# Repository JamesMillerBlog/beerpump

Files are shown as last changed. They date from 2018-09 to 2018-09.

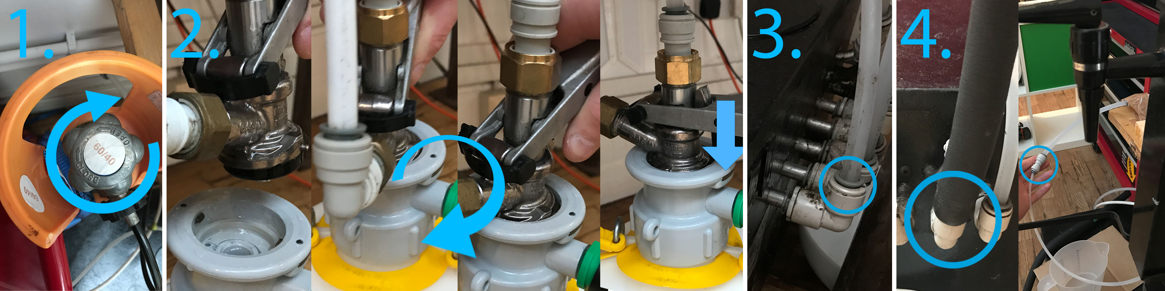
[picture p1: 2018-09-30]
Arduino-code/beerSetup.jpg

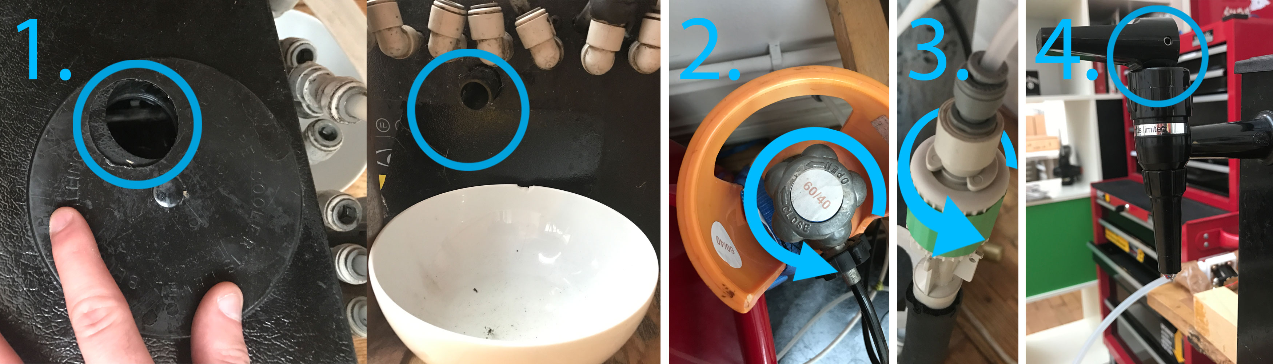
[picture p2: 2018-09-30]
Arduino-code/beerPour.jpg

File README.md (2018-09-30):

# BEER PUMP SET UP INSTRUCTIONS #

This is a tutorial on how to set up the beer pump hardware and software.

## Index ##
1. Code set up
2. Hardware set up
3. Beer equipment set up
4. How to operate
5. How to integrate software into the front end and hardware into the beer font
6. Troubleshooting

## 1. Code set up ##

### Code logic ###

This program is run on a node express server, which serves a web page that users interact with (on the touch screen), an admin web page (which allows the use of a manual override to all functions) and the control of the electronics that regulates the valve, monitors the volume of liquid passing through the beer font and switches the LEDs on/off.

The whole application is wrapped up inside of a gulp task management system, which creates a link that users can use to access the local host through a local network (I will go into more detail about this on the 'How to Operate' section). The flow of the application is as follows:

1. The express server is launched, the locally hosted accessible links are generated and the application begins constantly checking for the state of the liquid flow sensor pin.
2. When a user clicks on the "Pour Pint" button, this fires two web sockets, one that tells the application to open the valve and another that tells the application that it is pouring a pint. Upon receiving these sockets, the server sends a web socket back to the front end saying that the pint is being poured, then the front end responds by changing the interface.
3. As the beer is flowing, a sensor in the flow meter spins around on a 'windmill like' mechanism. As this mechanism spins around, the state of pin 2 of the Arduino goes from 1 - 0, the flow rate of the beer is calculated from the number of times the state of pin 2 **falls from 1 - 0** every 10th of a second. The ammount of beer in ml is then calculated based off of the flow rate.
4. When the "Stop Pint" button is pressed, it knows that a pint was pouring from the previous web socket message, so it sends a socket message to shut the beer valve + a socket message to state the pint has been paused and changes the interface to display "Resume Pint" + "Cancel Pint".
5. If the user presses "Resume Pint" the front end sends two socket messages to open the valve and tells the back end that the pint pouring has been resumed - the flow sensor will pick back up from where it left off.
6. If the user presses "Cancel Pint" this keeps the valve closed and all variables + functions in the backend are then reset, ready to pour a new pint.

### Downloading the code ###

Download this repository to a folder on your computer.

### Setup dependencies ###

* Install the latest version of Node onto your computer, older versions may not be able to run the dependencies needed to make the application work.

* Open Terminal from the applications folder

```
sudo npm install gulp -g
```

* Install Gulp globally

```
cd {YOUR/PATH/}
```

* Type cd into the terminal window, drag the folder that you've just downloaded into the window and press enter on your keyboard.

```
sudo npm install
```
* Type "sudo npm install" and press enter, this will install all necessary dependencies to run the application.

### Run the software ###

* Plug in the Arduino via the USB port (see below on how to set up the arduino's hardware)

```
gulp
```

* Type "gulp" into the terminal window, after a few seconds it will launch the application and open a web page. The opened web page is the touch screen interface which will need integrating with the front end, to access the admin page add the string "/admin" at the end of the url.

## 2. Hardware set up ##

### The Arduino code ###
*All the logic for the Arduino's are controlled in the node application above that you just installed, the code on the Arduino's allow the javascript application to send commands through the serial ports for the Arduino's to follow.*

***As the code is already install on both of the Arduino's, you should not need to follow the below steps, but I've included them incase there is a need for a re-installation.***

* Download Arduino software from arduino.org **(DON'T USE SOFTWARE FROM ARDUINO.CC OR INSTALLATION WILL FAIL)**
* Open the files "arduinoA.ino" and "arduinoB.ino", located in the "Arduino-code" folder, in the Arduino IDE.

* Select the "Arduino Mega or Mega 2560" from the "tools>board" menu, the correct serial port under "tools>port" and click upload. Make sure that the code for "arduinoA.ino" goes onto the Arduino labelled A and vice versa.

### Electronics ###

The below diagram is the electronic schematic for how to set up Arduino A which controls the valve, water flow meter + the payment LED Strip and Arduino B which controls the LED ring for the beer mat.

**Arduino A**

* The flow meter (pictured as a potentiometer) has three wires that connects to red to 5v; black to ground and yellow to pin 2.

* The valve is essentially an electro-magnet that is controlled by transistor that acts as a switch to a 12v power supply from the V-in pin on the Arduino. A resistor is used to protect the data pin from the current draw of the transistor that switches on the high voltage power supply and a diode is used to stop voltage spikes between ground and power lines that is created by switching an electro-magnet on/off.

* The LED strip is powered by the 5V 10A power supply, the data line of the strip goes into pin 7.

**Arduino B**

* The LED ring is powered by the 5V 10A power supply, the data line of the strip goes into pin 7. Make sure that the ground line is shared across both Arduino's and the power supply unit.

**IMPORTANT: A 12v power supply is attached to Arduino A's power jack, this raw supply line comes out of the V-in pin. Do not put anything that is powered by 5 volts on this line and do not attach this 12v line to any of the other Arduino pins or the 5v power supply.**

## 3. Beer equipment set up ##

### Connecting up the beer keg with the font. ###

The below image shows the order of how the beer serving equipment is set up, instructions to set this up are as below.



1. Make sure the gas bottle is closed by turning the handle on top clockwise.
2. Connect the gas bottle with an attached regulator to the keg, via the keg coupler. This is done by screwing the keg coupler down clockwise and then pressing the handle down to secure it firmly onto the keg.
3. Attach the beer line from the keg to interface with the cooler on the far left tube on the back of the cooler.
4. Link the beer line from the cooler (which is located 2nd from the far right on the back of the cooler), to the connector on the beer font and the set up is now complete.

### Interfacing the electronic hardware with the beer font ###

* The liquid flow meter and electronic valve are attached to the beer line in between the cooler and the beer font.
* The liquid flow meter must be placed before before the valve, to help prevent dripping of left over beer that is left between the valve and beer font nozzle when a pint has finished pouring.

### How to serve beer through the font ###



1. Make sure the cooler is filled with water, if it is not then pour water through the hole on the top and make sure there is an empty bowl underneath the black pipe located at the back of the cooler. Plug the power supply of the cooler into the wall to switch it on, the cooler will start making a fan sound and water will start to slowly trickle (periodically) from the black pipe.
2. Turn the handle of the gas bottle anti-clockwise to allow gas to pressurise the beer keg.
3. Turn the connector with the green label (located between the cooler and the beer font) anti-clock wise to open the line and allow beer to go to the beer font. This green labelled connector acts as a tap, it is **important to close this tap by turning the connector clockwise** if you want to open any of the beer lines for whatever reason, **if you don't then beer will pour out**.
4. If the electronic valve is not connected to the beer line, then you could now use the tap on the beer font to pour beer! Please see the 'How to operate' section to make beer pour out of the font.

### How to turn the beer serving equipment off ###
1. Unplug the cooler.
2. Turn the gas bottle's handle clockwise to close the gas supply off to the beer keg.
3. Turn the green handle attached to the cooler completely clockwise, to close the beer's supply to the beer font.

## 4. How to operate ##

### Link the touch screen to the local host ###
1. Make sure the iPod touch, the Mac Mini and any mobile device that you want connected to the admin page are all connected to the same wifi network. If there is not a wifi network to connect to, then create a local wireless network on the Mac Mini in the system settings and connect to that network on the iPod touch + admin mobile device.
2. Follow the steps in section 1 to open the software in terminal using the command "gulp". Once the software has been launched, a web browser will automatically be opened with the locally hosted web page. To open this page on the iPod touch, close the web page, go the the terminal window and find the link under "Access Urls" that appears next to "External:". The link should be something like: http://192.168.0.57:4000, remember this url for the next step.
3. On the iPod touch, type in the url to safari and press enter - the web page should now be displayed on the iPod touch.
4. Interacting with the interface will pour/pause/stop the beer flow from the tap.

### Accessing the admin page ###

1. To access the admin page, open the same url on the admin mobile device - but add the string "/admin" at the end (this will look something like: http://192.168.0.57:4000/admin).
2. The admin page has over-ride commands to control the beer fonts valve and LEDs, these can be used by touch the buttons on the interface.

**Notes**

As well as the override commands, there is a "Clean Out Pipes" function that pours 100ml of beer, this should be used when the beer pump has not been used for an hour or so - to help prevent foam.

## 5. How to integrate software and hardware ##

Making changes to the code is made very simple, as gulp has been configured to auto refresh the server and re-serve the html/css/js files every time a change has been made. Prior to making any changes, please make sure that gulp is running by following the steps in section 1 of this tutorial.

### Front End ###

**How to edit the front end code**

1. Make html changes to the touch screen on 'index.html' in the "Node-Server/app" directory.

2. Make html changes to the admin page on 'admin.html' in the "Node-Server/app" directory.

3. Make css changes to 'styles.scss' in the "Node-Server/app/scss" directory. Every time a change is saved, this will be automatically update "styles.css" located in the "Node-Server/app/css" directory (make sure that gulp is running whilst you make changes).

4. Make javascript changes to "script.js", located in the "Node-Server/app/js" directory.

5. All the sockets on the admin page control communicate with the back end to control the electronics, when building the interface on the touch screen, use these web sockets to control the electronics.

6. The sockets have been coded to mimic how the final app will be put together, do not try to fire more than one of the sockets attached to the buttons at the same time as this might confuse the node app controlling the electronics.

### Which sockets to integrate into the front end ###



The only sockets that should be included in the front end for the touch screen are the 4 circled in the above image from the admin page, and they should only be called in the user journey as numbered (call the socket attached to the "Payment blink" button when a payment is required, then call the socket attached to the "Beer mat blink" button when the user needs to put their beer on the mat, etc).

**How to edit the back end code**

Open the "index.js" file located in the "Node-Server" directory.

**How to put code onto a publicly accessible server**

This is not necessary for the project, but if we wanted to do this we would need to run this application on a server that could support node. This would be something that Ben could help with.

### Integrate hardware into the beer font ###

**Beer Line**

Remove the beer line that is attached to the nozzle in the test unit, and put it into the nozzle on the new beer font.

**LEDs**

There should be two slots inside of the font which will have space for both the LED strip and LED circle. Once the font has been produced, you will need to place the LED circle into its slot for the beer mat and see how many LEDs within the strip will fit for the payment lighting.

## 6. Troubleshooting ##

### Beer equipment ###

**Too much foam per pint**

The green labelled connector which is attached to a pipe, located at the back of the cooler is a valve. By turning the connector clockwise slowly, this will slightly close the valve, reduce the speed of the beer pouring from the font and therefore help reduce the foam.

**Foam sputtering out of nozzle**

This is because the keg is empty, replace the keg to resolve this issue

**Beer tap not pouring beer**

When the handle for the beer tap is opened, this will not make beer pour as there is an electronic valve stopping the liquid in the beer line. To pour beer, click on the "Pour Pint" button on the touch screen.

**Pour Pint button is not pouring a pint**

If clicking on the "Pour Pint" button is not pouring a pint, then check if the page has fully loaded. If it is not, then this means that the sockets have not been initiated and back end will not be receiving any socket messages to activate the valve. Refresh the web page manually to resolve this.

**Web sockets are working, but beer is still not pouring**

If web sockets are working correctly then check if the green labelled connector which located at the back of the cooler is open, by turning the connector anti-clockwise.

**How to remove and replace a keg**

1. Turn the handle on the gas canister clockwise to close off the gas supply.

2. Turn the green labelled connector attached to the cooler clockwise to close the valve.

3. Lift the handle of the keg coupler up and turn it anti-clockwise to detach it from the keg (expect a little bit of compressed gas to escape). Put the keg coupler onto the new keg and turn it clockwise to attach it onto the keg, press handle of the coupler down to fix it to the keg.

4.Turn the gas canister handle + green labelled cooler connector anti clockwise and the beer can now be poured from the new keg.

**How to detach the beer line pipes**

1. Push the pipe into the pipe connector
2. Push the dark grey ring down into the connector
3. Pull the pipe out of the connector whilst pushing the dark grey ring down.

**How to replace a gas canister**

1. Turn the handle on the gas canister clockwise as tightly as possible to completely close off the gas supply.
2. Turn the cog shaped handle which connects the gas supply to the gas regulator anti-clockwise to detach it from the gas canister.
3. Place the cog shaped handle back onto the gas canister and turn it clock wise to close it.
4. Open the gas canister's valve by turning it anti-clock wise and the gas canister should now be working correctly.

### Code ###

**Terminal error when I try to pour a pint**

If terminal displays an error like: "TypeError: Cannot read property 'write' of undefined", then this means that the Arduino is not plugged in, plug the Arduino into the computer USB and this will resolve the issue.

**Web page not refreshing when restart the node server**

Sometimes when the node server is restarted, the web page does not auto-refresh properly - in this scenario you will need to press the refresh button.

**I want to run the application without gulp**

In terminal navigate to "Node-Server" directory and then type "node index.js". This will launch a local server which you can access by typing "http://localhost:3000" into your browser url bar.

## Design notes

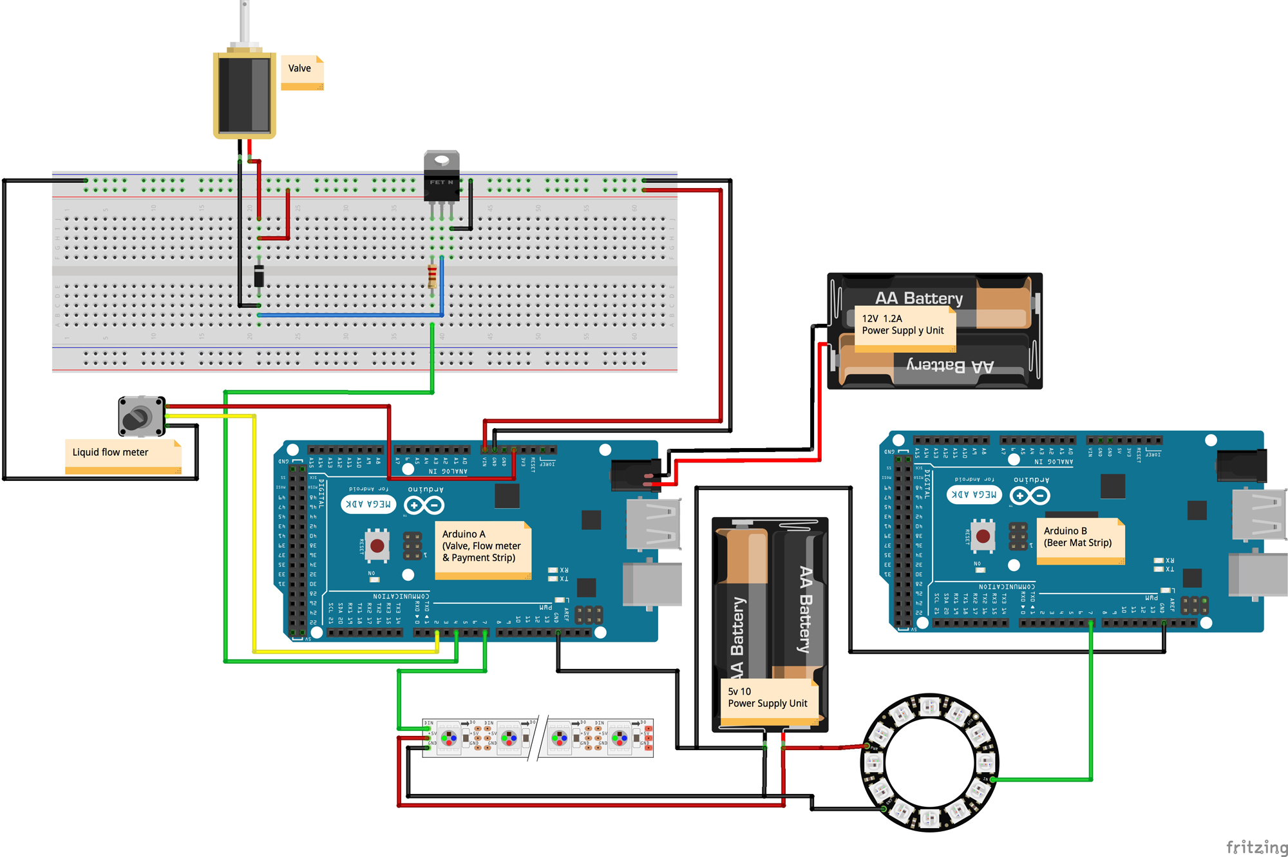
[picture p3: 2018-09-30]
Arduino-code/Schematic.jpg

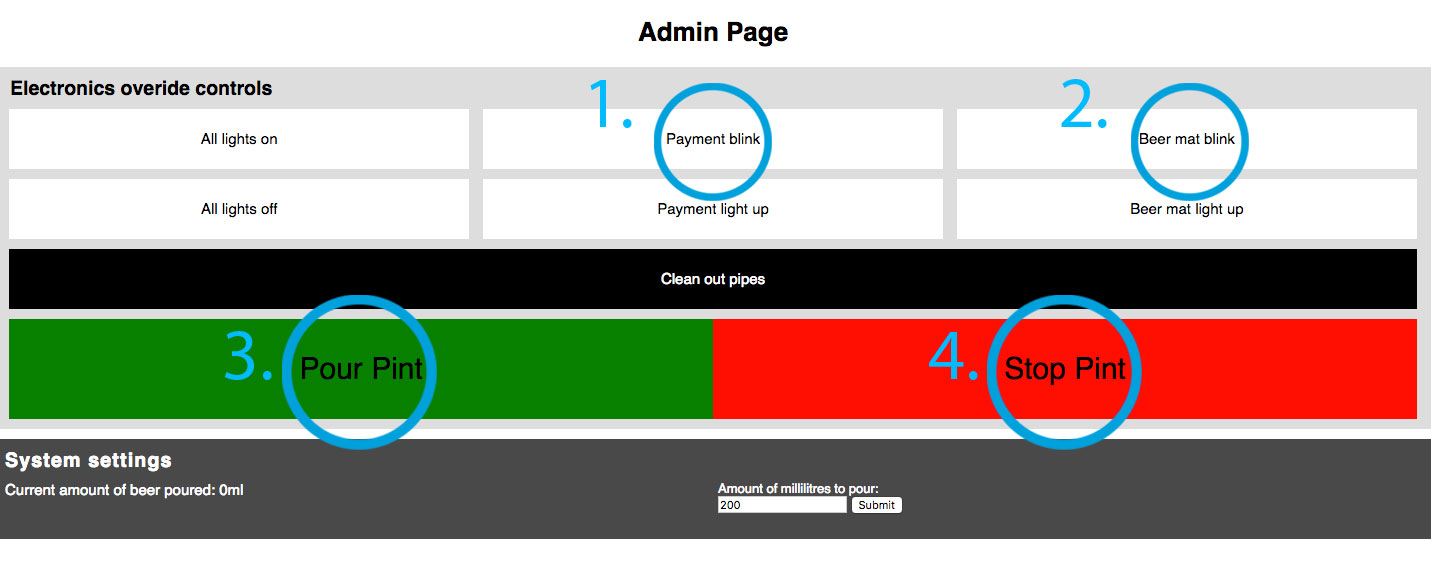
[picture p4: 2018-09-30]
Arduino-code/adminSocketsToUse.jpg

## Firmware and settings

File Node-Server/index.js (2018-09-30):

//*** STATIC VARIABLES ***//
//1. Server init
var app = require('express')(),
	http = require('http').Server(app),
	io = require('socket.io')(http),
	previousCommand,
	previousTwoCommand,
	interfaceControl = 'startUp';
//2. Arduino init
var five = require("johnny-five"),
	//declare two boards: A = beer pump/izettle lights, B = beer mat lights
	boards = new five.Boards(["A", "B"]),
	//array to store arduino pin data
	j5 = {},
	pixel = require("../lib/pixel.js");
//3. Arduino valve + sensor variables
var oldSensorState = 0,
	sensorInterval,
	lightInterval,
	pintInterval,
	intervalMilliSecondCount = 10,
	loopInterval = 10,
	pulseCount=0,
	flowRate = 0,
	flowMillilitres = 0,
	totalMillilitres = 0,
	startTime,
	oldTime = 0,
	repeater,
	barBlue = 204,
   	barGreen = 148,
   	barRed = 80,
    speed = 6,
    blueIncreaser = 1 * speed,
    greenIncreaser = (barGreen/barBlue)*speed,
    redIncreaser = (barRed/barBlue)*speed,
    currentBlue = 0,
	rawGreen = 0,
	rawRed = 0,
	currentRed = 0,
	currentGreen = 0,
	colorReached = false,
	resume = false,
	resetTimer = false,
	devMode = true,
	valveChecker = false,
	totalOldMillilitres = 0;

//*** ADJUSTABLE VARIABLES ***//
var calibrationFactor = 6, //change this to adjust the sensitivity of the flow sensor
	pint = 550, //change this to 550(ml) for final installation
	pipeCleaner = 100;

//*** SET UP HTML/CSS/JS FILES WITH THE SERVER ***//
var serveFileLocations = [
	//admin
	'/admin', '/admin/css/styles.css', '/admin/js/script.js',
	//app
	'/', '/app/js/socket.io.js', '/app/js/scripts.socket.js', '/app/js/scripts.js', '/app/css/styles.css', '/app/audio/beep.mp3',
	//images
	'/app/images/page1a.jpg', '/app/images/page1b.jpg', '/app/images/page1c.jpg', '/app/images/page1d.jpg', '/app/images/page1e.jpg', '/app/images/page1f.jpg', '/app/images/page1g.jpg',
	'/app/images/page2.jpg', '/app/images/page3.jpg', '/app/images/page4.jpg', '/app/images/page5.jpg', '/app/images/page6.jpg', '/app/images/page7.jpg', '/app/images/page8.jpg', '/app/images/page9.jpg', '/app/images/page10.jpg', '/app/images/page11.jpg', '/app/images/page12.jpg', '/app/images/page_error.jpg',
	'/app/images/loading.gif', '/app/images/loading2.gif'
];
var serveFiles = [
	//admin
	'/admin/index.html', '/admin/css/styles.css', '/admin/js/script.js',
	//app
	'/app/', '/app/js/socket.io.js', '/app/js/scripts.socket.js', '/app/js/scripts.js', '/app/css/styles.css', '/app/audio/beep.mp3',
	//images
	'/app/images/page1a.jpg', '/app/images/page1b.jpg', '/app/images/page1c.jpg', '/app/images/page1d.jpg', '/app/images/page1e.jpg', '/app/images/page1f.jpg', '/app/images/page1g.jpg',
	'/app/images/page2.jpg', '/app/images/page3.jpg', '/app/images/page4.jpg', '/app/images/page5.jpg', '/app/images/page6.jpg', '/app/images/page7.jpg', '/app/images/page8.jpg', '/app/images/page9.jpg', '/app/images/page10.jpg', '/app/images/page11.jpg', '/app/images/page12.jpg', '/app/images/page_error.jpg',
	'/app/images/loading.gif', '/app/images/loading2.gif'
];
//loop to call the file server function
for(var x = 0;x<serveFileLocations.length;x++) fileServer(x);
//serves all files from both of the above arrays
function fileServer(x){
	app.get(serveFileLocations[x], function(req, res){
	  res.sendFile(__dirname + serveFiles[x]);
	});
}
//app.use(express.static('app'));
//app.use("/app", express.static('app'));

//*** SOCKETS ***//
//When a user connects to the local host
io.on('connection', function(socket){
	console.log('a user connected');
	//socket to control the pump
	socket.on('pumpSwitcher', function(pumpVal){
		console.log('message: ' + pumpVal);
		//if the previous command isn't the same as the current one, activate pump function
		if(previousCommand != pumpVal) {
			pintActuator(pumpVal);
			previousCommand = pumpVal;
		}
		//previous command is updated to latest command, this stop multiples of the same message being sent
	});
	//When the interface is telling the server if it is paused/pouring/stopped
	socket.on('interfaceController', function(msg){
		//Store the current interface position + stop multiple of the same command
		if(interfaceControl != msg){
			//activates a feature to create smoother led colour transition when resuming a pint pour
			if(previousTwoCommand == "pintPaused" && interfaceControl == "pintPouring") resume = true;
			//if not resuming a pour then set to false
			else resume = false;
			//get message from socket and put in a global variable
			interfaceControl = msg;
			//activate leds
			activateLeds(msg);
			// console.log("interfaceControl = " + interfaceControl);
		}
		// console.log("previous command was = " + previousTwoCommand);
		// logic to store the last socket message to work out if the pint is resuming a pour from a paused state
		if(interfaceControl != previousTwoCommand) previousTwoCommand = interfaceControl;
	});
	//socket from the front end to receive how many ml of beer will pour from the nozzle
	socket.on('beerSettings', function(settings){
		//update adustable pint variable
		pint = settings;
		//emit the new beer setting to the front end (confirming that it has been received ok)
		io.emit('beerSettings', pint);
		// console.log("new pint value is = " + pint);
	});
	//socket from the front end for app settigns
	socket.on('beerAdmin', function(response){
		//emit the new beer setting to the front end (confirming that it has been received ok)
		io.emit('beerAdmin', response);
	});
	//log when a user has disconected
	socket.on('disconnect', function(){
    	console.log('user disconnected');
  	});
});
//express server running on local host 3000 (will be local host 4000 using gulp)
http.listen(3000, function(){
  console.log('listening on *:3000');
});
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
